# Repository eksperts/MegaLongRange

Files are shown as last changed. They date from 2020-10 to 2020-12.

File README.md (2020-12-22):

# MegaLongRange
The 7'' long range quadcopter frame with 3D printed accessories
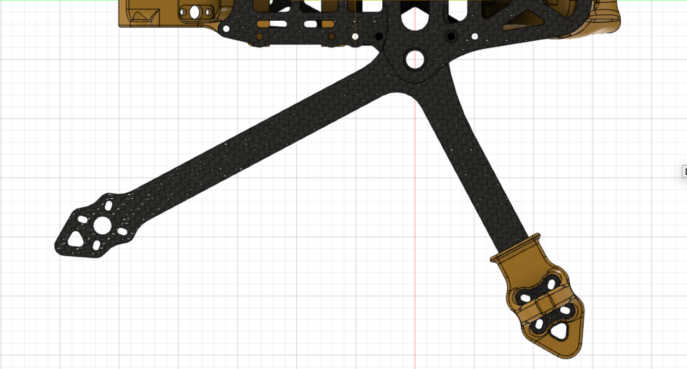
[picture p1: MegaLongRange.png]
MegaLongRange sketch


## How does it fly?
GoPro Hero 7 Black, no stabilisation on BrotherHobby 2808 1500kv motors, 1800mAh 6S LiPo: [Watch on YouTube](https://www.youtube.com/watch?v=DcVzKVmMOWc)

## Additional hardware required
* Two (2) M3x28mm aluminium standoffs, external diameter 5mm
* Four (4) M3x20mm aluminium standoffs, external diameter 5mm
* Twelve (12) M3x8mm screws to secure the standoffs to carbon fiber plates
* Two (2) "double" chainring bolts (different size may be needed if you change any plate or arm thickness)
  * the bottom cylinder needs to be about 8mm tall, excluding the base
  * the top screw needs to be exactly 10mm tall, excluding the head

## Weight estimates
All carbon fiber parts plus hardware.

**6mm** arms: **137g**

**5mm** arms: **117g**

**4mm** arms: **97g**

For canopy and antenna mount prints, add another **20-30g**.

## Suggested parts that fit the 3D prints
* The canopy is designed for DJI FPV camera, so it would make sense to go with a DJI FPV Air Unit.
* If using a DJI FPV Air Unit, you'll need two (2) [TBS MMCX-to-SMA pigtails](https://www.team-blacksheep.com/products/prod:sma_mmcx9_pigtail) for the antenna mount.
* A [TBS Crossfire Diversity Nano RX](https://www.team-blacksheep.com/products/prod:xf_nano_div_rx) with two (2) [TBS Crossfire Immortal T antennas](https://www.team-blacksheep.com/products/prod:xf_immortal_t_v2_s) (See also [extended](https://www.team-blacksheep.com/products/prod:xf_immortal_t_v2_e) and [extra extended](https://www.team-blacksheep.com/products/prod:xf_immortal_t_v2_ee) versions).

## Custom Motor Mixes
Since this is a dead-cat frame, you might find it easier to use custom motor mixing to get your tune right. I did the math for you, so here goes.

This is what I have on my build, with reversed motors ("props out"):
```
mixer custom
mmix reset
mmix 0 1 -0.74 0.728 -1
mmix 1 1 -1 -0.728 1
mmix 2 1 0.74 0.728 1
mmix 3 1 1 -0.728 -1
```

## References
The design of this frame was inspired by, and it retains signature features from the [MiniLongRange 5'' by Dave_C](https://www.thingiverse.com/thing:4584851).

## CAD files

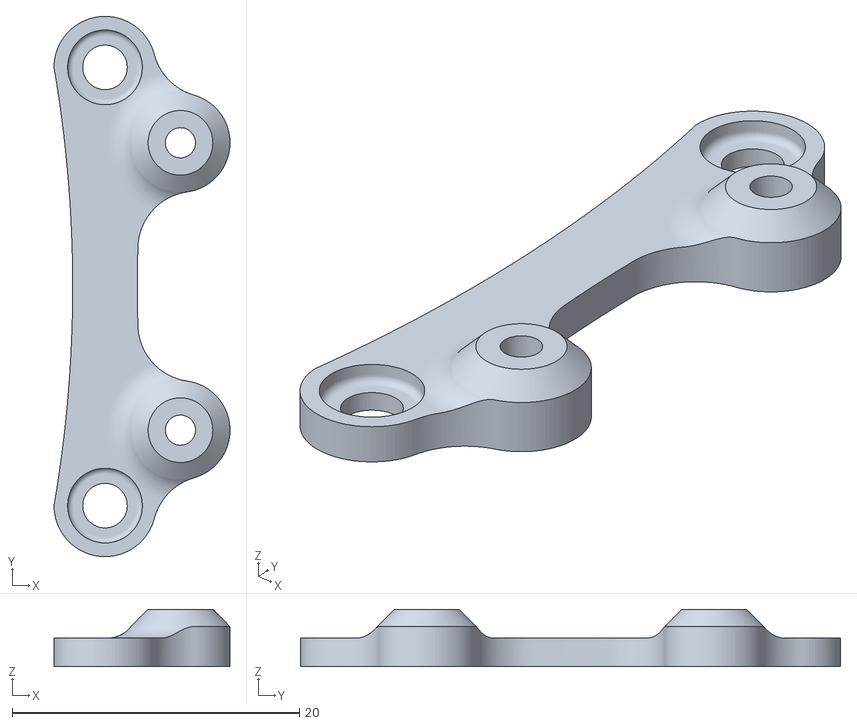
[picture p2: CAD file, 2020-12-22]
Accessories/MegaLR-stack_bracket_30-20_recessed.stl
12.2 x 37.6 x 4.00

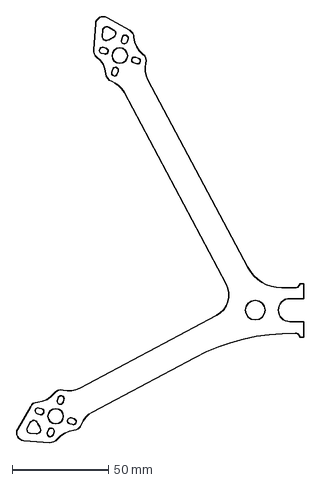
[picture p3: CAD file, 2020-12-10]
DXF/02_MegaLR-arm_6mm.dxf
149.0 x 221.2 mm

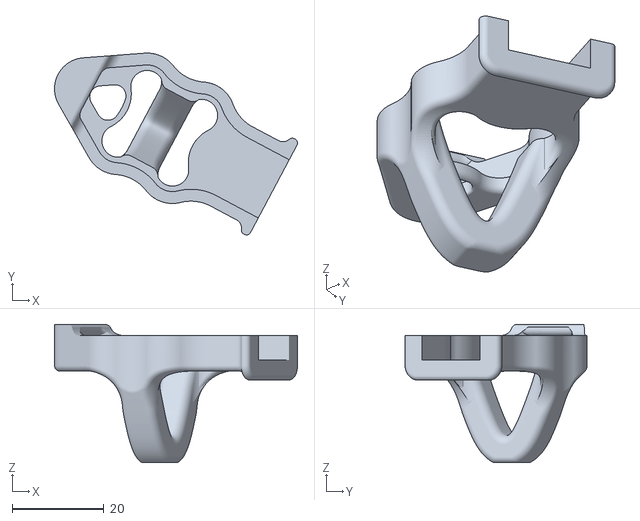
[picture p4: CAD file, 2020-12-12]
Accessories/MegaLR-landing-pad-with-lip_5mm-arms.stl
53.1 x 39.7 x 30.2

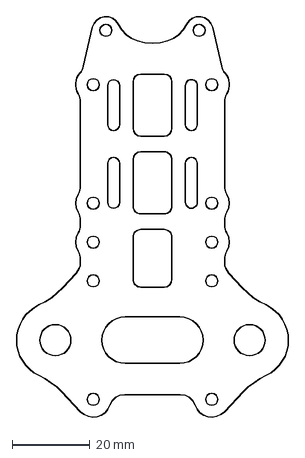
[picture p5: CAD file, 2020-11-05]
DXF/03_MegaLR_middle-plate_2mm.dxf
70.0 x 103.5 mm

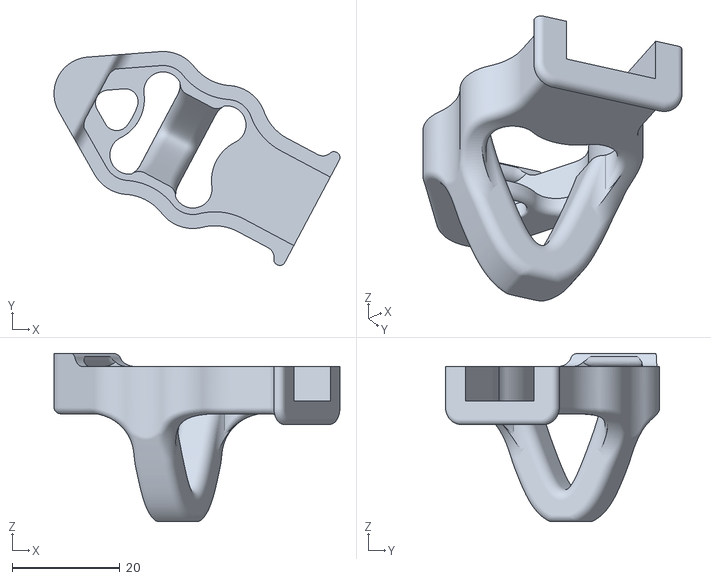
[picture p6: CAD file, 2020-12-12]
Accessories/MegaLR-landing-pad-with-lip_6mm-arms.stl
53.1 x 39.7 x 31.2

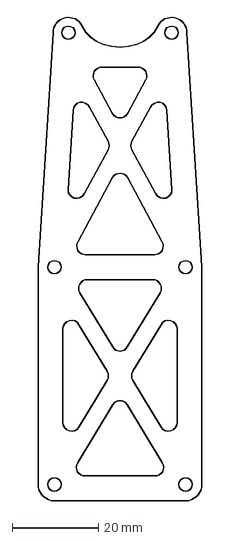
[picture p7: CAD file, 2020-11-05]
DXF/04_MegaLR_top-plate_2mm.dxf
38.0 x 112.6 mm

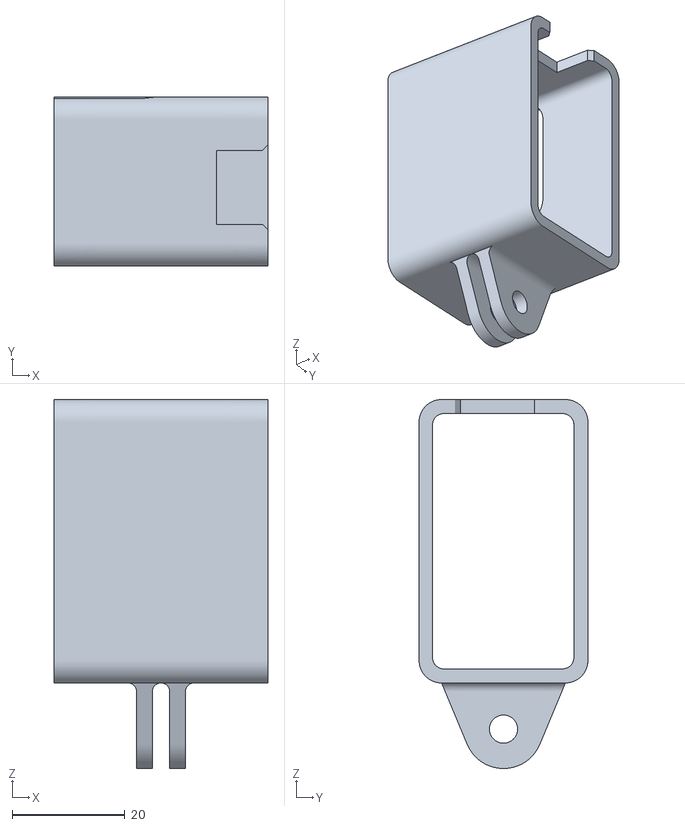
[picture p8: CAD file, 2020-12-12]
Accessories/MegaLR-GoPro-Hero-567-mount.stl
38.0 x 30.0 x 65.5

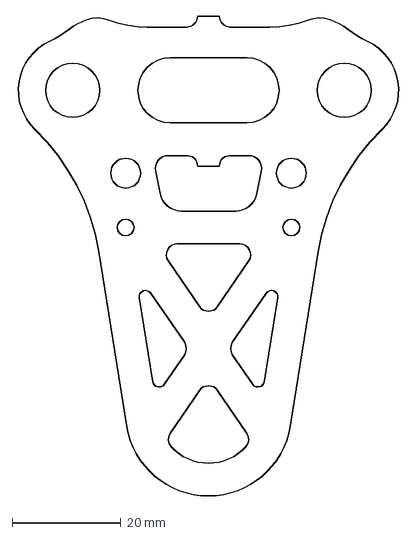
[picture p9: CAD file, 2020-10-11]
DXF/01_MegaLR_bottom-plate_2mm.dxf
70.8 x 88.3 mm

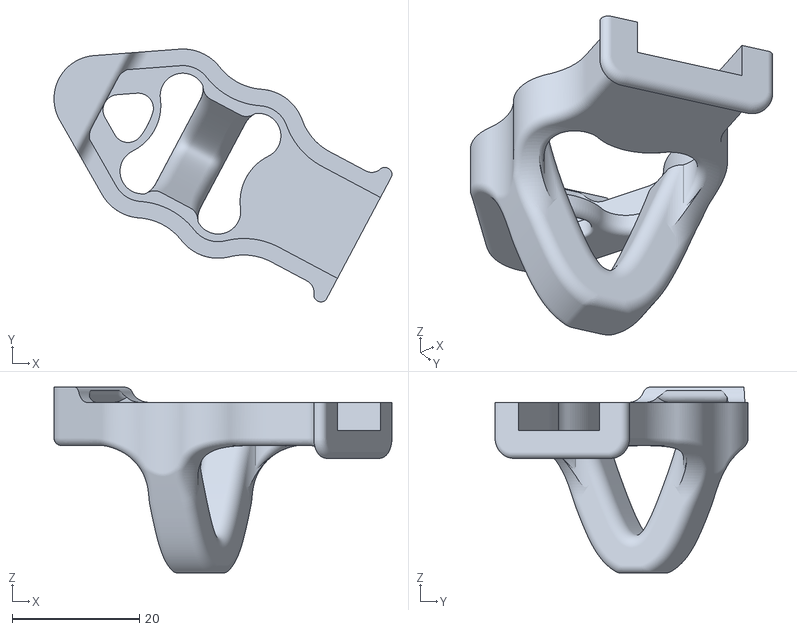
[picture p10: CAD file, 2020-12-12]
Accessories/MegaLR-landing-pad-with-lip_4mm-arms.stl
53.1 x 39.7 x 29.2

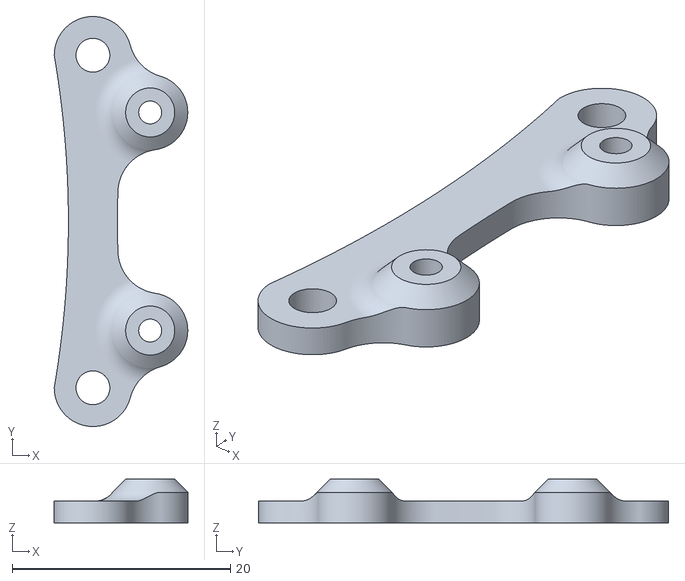
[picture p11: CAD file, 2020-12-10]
Accessories/MegaLR-stack_bracket_30-20.stl
12.2 x 37.6 x 4.00

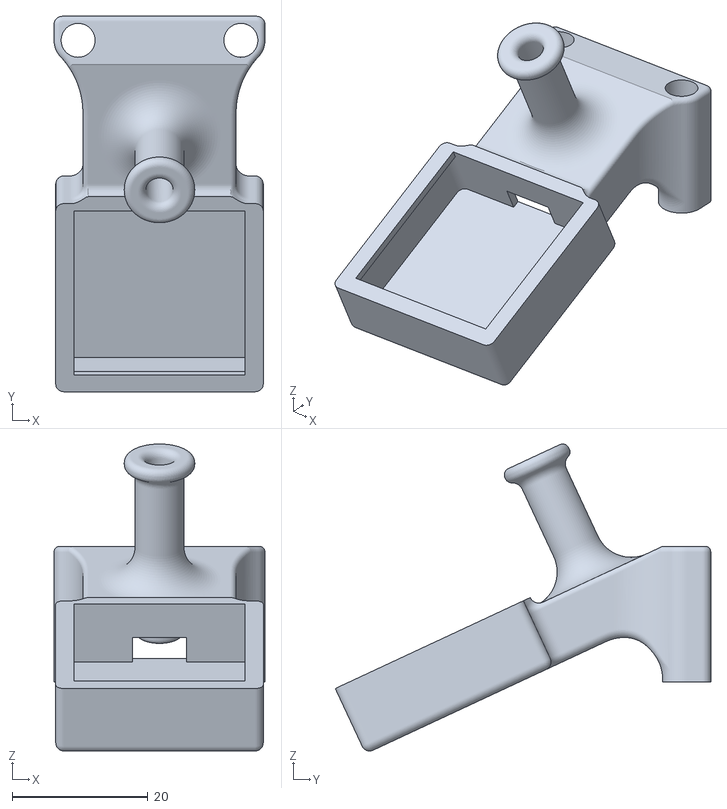
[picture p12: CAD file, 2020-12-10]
Accessories/MegaLR-antenna_mount-Vista-BN880.stl
31.1 x 55.4 x 45.3

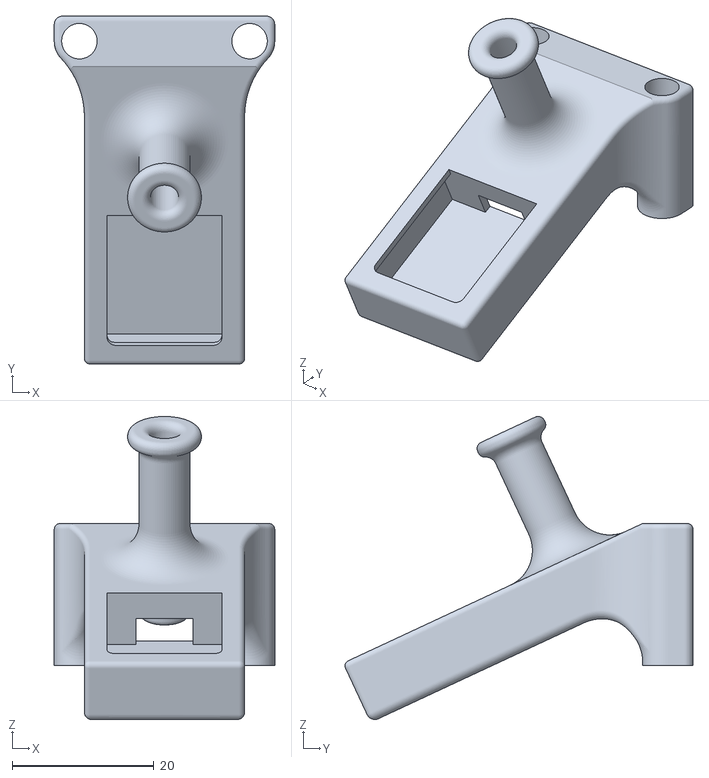
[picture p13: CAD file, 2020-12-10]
Accessories/MegaLR-antenna_mount-Vista-GPS.stl
31.1 x 49.1 x 42.7

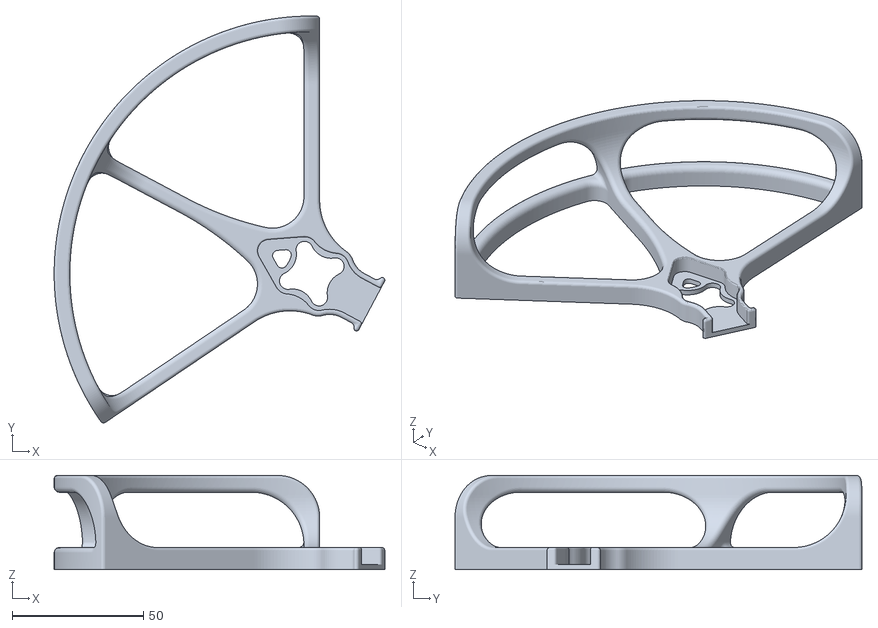
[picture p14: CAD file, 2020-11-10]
Accessories/MegaLR-prop-guard.stl
125.8 x 154.8 x 35.8

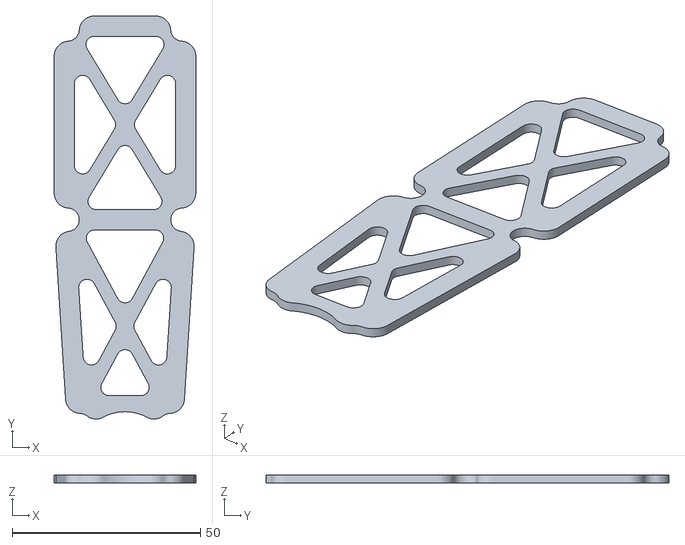
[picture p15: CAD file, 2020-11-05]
Accessories/MegaLR-battery-pad-top-plate.stl
37.6 x 107.0 x 2.00

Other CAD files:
Accessories/MegaLR-antenna_mount-DJI-GPS.stl
Accessories/MegaLR-dji-air-unit-mount-front.stl
Accessories/MegaLR-dji-air-unit-mount-back.stl
Accessories/MegaLR-xt60-standoff-mount.stl
Accessories/MegaLR-battery-pad-bottom-plate.stl
Accessories/MegaLR-gps-arm-mount-20mm.stl

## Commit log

2020-10-11 adding V1 DXF and STL files
    [01_MegaLR_bottom-plate_2mm.dxf, 02_MegaLR-arm_6mm.dxf, 03_MegaLR_middle-plate_2mm.dxf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]
2020-10-12 made holes bigger to accept 5mm wide standoffs
    [MegaLR-antenna-mount-DJI.stl]
2020-10-12 improved the tail mount for easier printing and increased durability
    [MegaLR-antenna-mount-DJI.stl]
2020-10-12 fixed dimensions and more work on printability
    [MegaLR-antenna-mount-DJI.stl]
2020-10-13 adding a battery pad for the top plate
    [MegaLR-battery-pad-top-plate.stl]
2020-10-13 adding a battery pad for bottom plate
    [MegaLR-battery-pad-bottom-plate.stl]
2020-10-14 adding GPS and XT60 mounts
    [MegaLR-gps-arm-mount-20mm.stl, MegaLR-xt60-standoff-mount.stl]
2020-10-18 adding DJI FPV air unit TPU mount
    [MegaLR-dji-air-unit-mount-back.stl, MegaLR-dji-air-unit-mount-front.stl]
2020-10-30 added a new tail mount for GPS, DJI and Immortal T
    [MegaLR-antenna_mount-DJI-GPS.stl]
2020-11-05 altered two plates to better accommodate DJI FPV air unit antennas. TODO: modify tail mounts
    [03_MegaLR_middle-plate_2mm.dxf, 04_MegaLR_top-plate_2mm.dxf]
2020-11-05 updated prints to fit the new plates
    [MegaLR-antenna_mount-DJI-GPS.stl, MegaLR-battery-pad-top-plate.stl]
2020-11-05 removed a tail mount
    [MegaLR-antenna-mount-DJI.stl]
2020-11-05 changed approach, remade the plates and prints differently
    [03_MegaLR_middle-plate_2mm.dxf, 04_MegaLR_top-plate_2mm.dxf, MegaLR-antenna_mount-DJI-GPS.stl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]
2020-11-06 updated README with custom motor mixes
2020-11-06 updated tolerances on arms
    [02_MegaLR-arm_6mm.dxf]
2020-11-10 adding 7'' prop guards
    [MegaLR-prop-guard.stl]
2020-11-12 adding landing pad / arm guard STL
    [MegaLR-landing-pad.stl]
2020-11-29 added a shorter canopy for those who opt for 4mm thick arms
2020-12-04 figured out custom motor mixes, adding info
2020-12-10 fixed arm tolerances (again?), added 3 new prints
    [02_MegaLR-arm_6mm.dxf, MegaLR-antenna_mount-Vista-BN880.stl, MegaLR-antenna_mount-Vista-GPS.stl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]
2020-12-12 added more prints
    [MegaLR-GoPro-Hero-567-mount.stl, MegaLR-landing-pad-with-lip_4mm-arms.stl, MegaLR-landing-pad-with-lip_6mm-arms.stl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]
2020-12-12 added 2 more prints for 5mm tall arms
    [MegaLR-landing-pad-with-lip_5mm-arms.stl]
2020-12-22 added another STL, updated readme
    [MegaLR-stack_bracket_30-20_recessed.stl]
